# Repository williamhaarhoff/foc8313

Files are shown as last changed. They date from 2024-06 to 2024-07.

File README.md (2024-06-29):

# foc8313
This board was inspired by [Foc-Ctrl-Lite](https://github.com/peng-zhihui/Ctrl-FOC-Lite). FOC8313 is a highly compact, feature rich, daisy-chainable,  field oriented control board based around the DRV8313 3 phase half bridge driver. This board is highly configurable and upgradeable, and includes all the manufacturing files required start producing controllers for $\approx$ $20/board
|Front|Back|
|--| --|
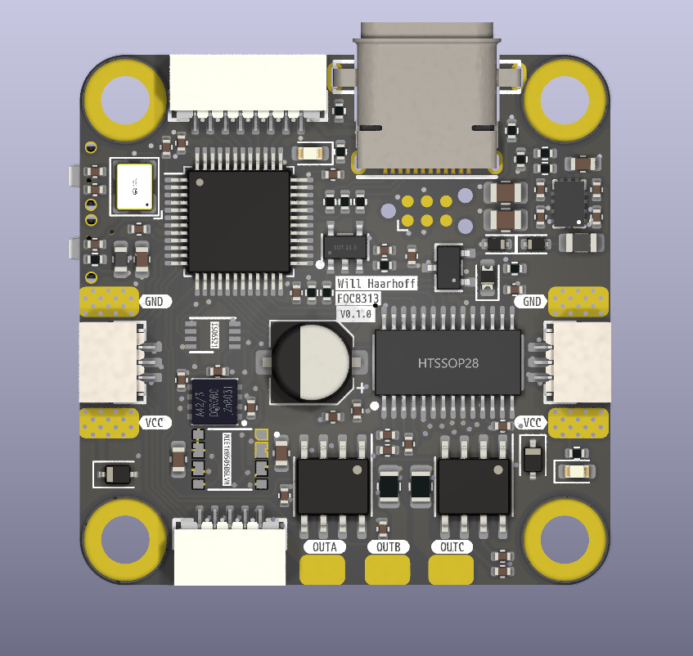
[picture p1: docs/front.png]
front
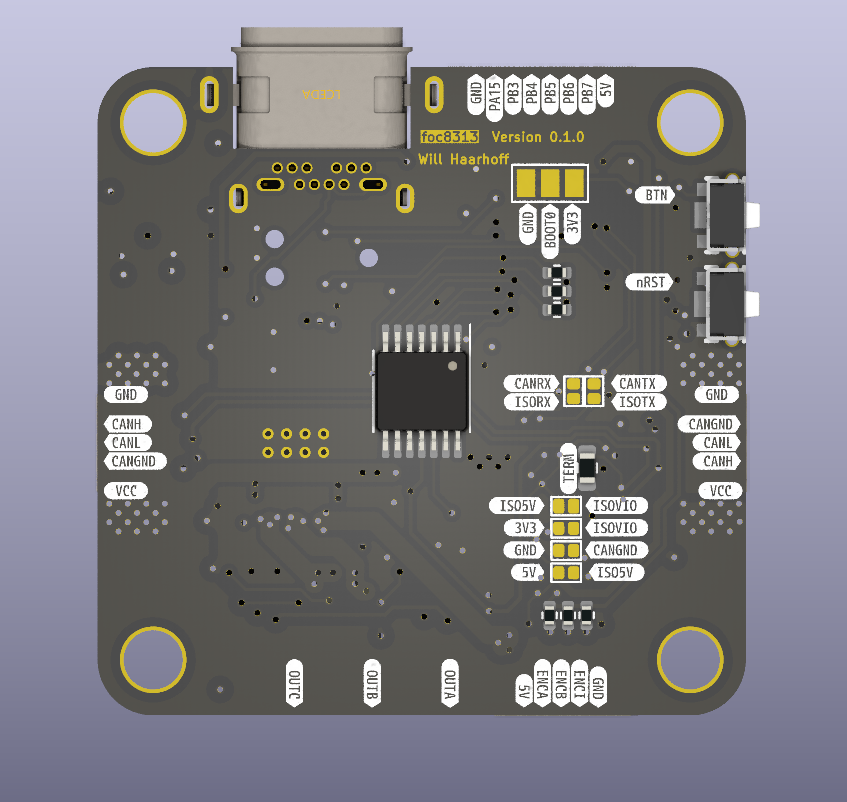
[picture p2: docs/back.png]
back
| | |

## Features:
 - Highly compact 35x35mm outline
 - 29x29 square M3 hole pattern
 - 12V to 35V operating range
 - 3.5A max per phase current
 - Onboard STM32F103CBTx microcontroller
 - Based on the DRV8313 3 phase half bridge driver
 - 2 x INA240A2D high side current sense amplifiers
 - 1 x AS5047D back mounted hall effect encoder
 - EEPROM to store configurations / calibrations etc. 
 - Daisy chainable power and CAN
 - Programmable with USB-DFU or StLink - 6 pin tag connect
 - Auxilliary encoder/Timer port with 5V and GND
 - Auxilliary SPI/GPIO and I2C/UART port with 5V and GND
 - Easily upgradable for isolated CAN (3 wire)
 - Extremely compact isolated CAN
 - JLC manufacturing files included
 - Cost optimised for PCBA with JLCPCB (as few extended components as possible)
 - Most basic variant costs $\approx$ $20 per board (for 10 PCBs at JLCPCB)
 - Predominantly single sided design allows for cost effective single sided PCBA, easy hot plating for rework, easy configuration with jumpers

| Top | In1 |
|--| --|
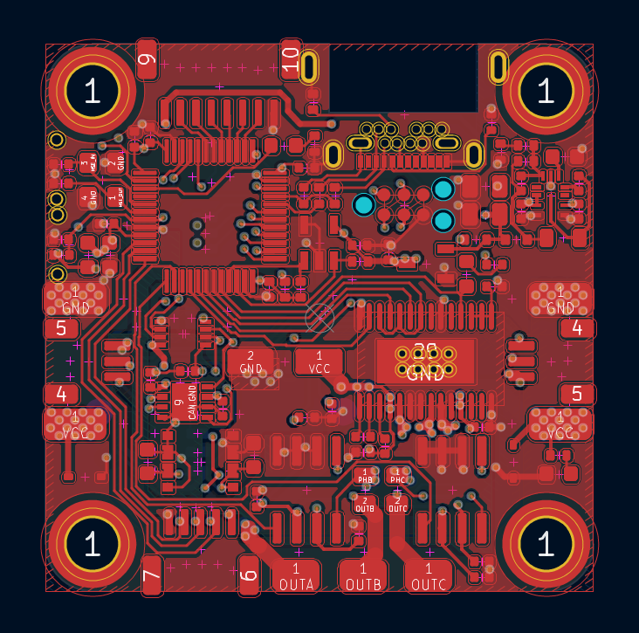
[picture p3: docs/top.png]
top
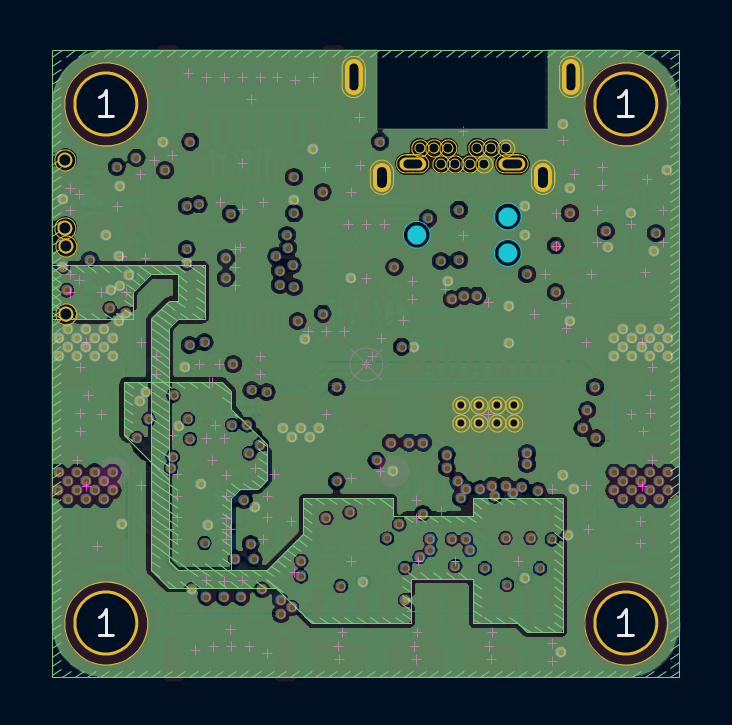
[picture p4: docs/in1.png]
in1
|||
|In2 | Bottom|
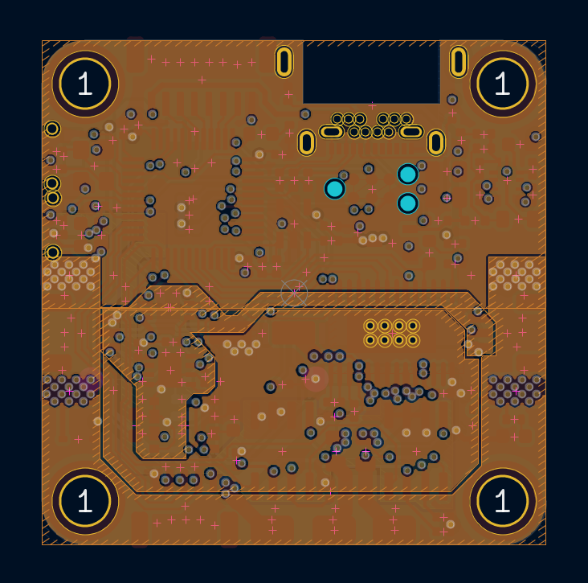
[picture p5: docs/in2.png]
in2
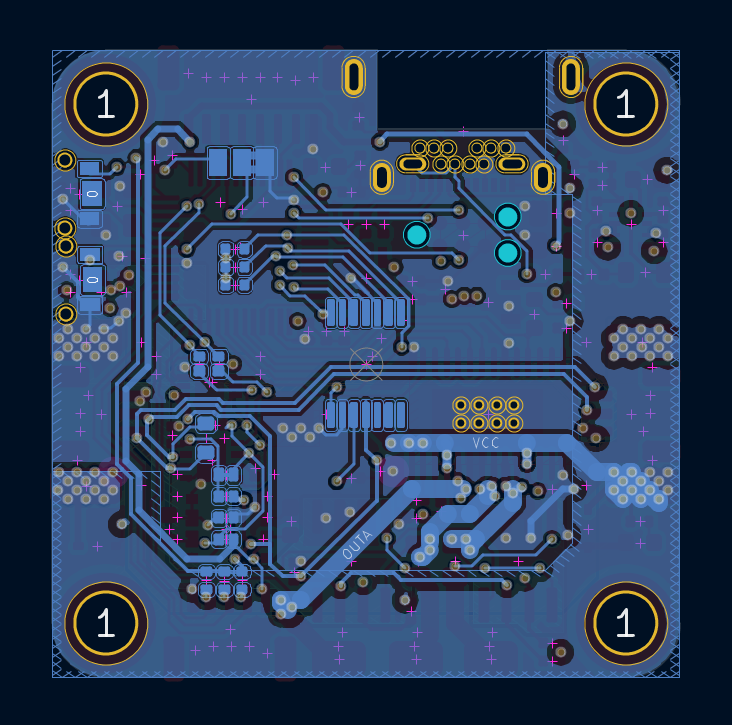
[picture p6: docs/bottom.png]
bottom
|||

# PCBA - Cost Scaling:
| Version | Colour | Finish | Assembly | Quantity | Unit price | Extended Price |
| ----- | ---- | --- | ----- | ----- | ---- | --- |
| v1.0 | Black  | Enig | Standard T&B  | 15 |$30.8 | $462.57 |
| v1.0 | Black  | Enig | Standard Top  | 15 |$24.3 | $364.22 |
| v1.0 | Black  | HASL | Standard Top  | 10 |$24.75 | $247.51 |
| v1.0 | Black  | Enig | Standard T&B  | 100 |$16.78 | $1678.39 |
| v1.0 | Green  | HASL | Economic Top  | 2 |$53.45 | $106.89 |
| v1.0 | Green  | HASL | Economic Top  | 5 |$30.28 | $151.40 |
| v1.0 | Green  | HASL | Economic Top  | 10 |$20.48 | $204.81 |
| v1.0 | Green  | HASL | Economic Top  | 15 |$19.2 | $288.48 |
| v1.0 | Green  | HASL | Economic Top  | 30 |$15.6 | $468.48 |
| v1.0 | Green  | HASL | Standard Top  | 100 |$12.98 | $1297.77 |
| v1.0 | Black  | Enig | No ICs Top | 10 |$15.9 + | $159.37 |
| v1.0 | Black  | Enig | No ICs Top | 15 |$12.9 + | $193.44 |

# ICs:
15x @LCSC: 215.22 -> 14.33
10x @LCSC: 146.71 -> 14.6

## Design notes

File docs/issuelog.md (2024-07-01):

# v0.1.0 - issues
  - USB incorrect outline
  - USB incorrect pinout 
  - 3.3v vs 3v3 mixed incorrect nets
  - LDO incorrect pinout
  - ISO power vselect incorrect
  - Some boards had buck converter shorts
  - ISO power too close to CAN IC
  - Capacitor too close to CAN IC
  - Diode inline with buck converter output
  - Vcc power plane gets choked and should be wider
  - Daisy chained GND also gets choked and should be wider
  - Plane clearance is very small
  - Isense resistors could be bigger
  - No vbus measurement
  - Silk screen too small
  - Not a fan of the yellow or red LEDs
  - Provision pullups for external ABI interface?

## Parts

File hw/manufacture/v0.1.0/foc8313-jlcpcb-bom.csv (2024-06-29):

Comment | Designator | Footprint | LCSC Part Number
100n | C1,C2,C3,C4,C6,C7,C12,C20,C21,C22,C24,C25,C26,C27,C28,C29,C33,C34,C35,C36 | C_0402_1005Metric | C307331
1u | C5,C15 | C_0603_1608Metric | C15849
220n | C8 | C_0402_1005Metric | C16772
2.2u | C9 | C_0805_2012Metric | C377773
22n | C10,C11 | C_0402_1005Metric | C1532
4.7p | C13 | C_0402_1005Metric | C1567
22u | C14 | C_0805_2012Metric | C45783
18p | C16,C17 | C_0402_1005Metric | C1549
2.2u | C18 | C_0402_1005Metric | C12530
10n | C23 | C_0402_1005Metric | C15195
47u | C30 | CP_Elec_5x5.7 | C7471868
22u | C37,C38 | C_0603_1608Metric | C59461
36V | D1,D3 | D_SOD-323 | C92677
RB521S30T1G | D2,D6 | D_SOD-523 | C145179
LED | D4 | D_0603_1608Metric | C2286
WHITE | D5 | LED_0603_1608Metric | C2290
YELLOW | D7 | LED_0603_1608Metric | C72038
MountingHole_Pad | H1,H2,H3,H4 | 2x4 | no_part_number
MountingHole_Pad | H5,H6,H9 | 2x3 | no_part_number
MountingHole | H7,H8,H10,H11 | MountingHole_3.2mm_M3_DIN965_Pad_TopOnly | no_part_number
Tag Connect | J1 | Tag-Connect_TC2030-IDC-NL_2x03_P1.27mm_Vertical | no_part_number
Encoder | J2 | CONN-SMD_5P-P1.00_MEGASTAR_ZX-SH1.0-5PWT | C7430447
CAN | J3,J4 | CONN-SMD_AFC10-S03QCA-00 | C2764182
GPIO | J6 | CONN-SMD_8P-P1.00_MEGASTAR_ZX-SH1.0-8PWT | C7430450
* | JP1 | SolderJumper-3_P1.3mm_Bridged2Bar12_Pad1.0x1.5mm | no_part_number
* | JP2,JP4,JP5,JP6,JP7 | jumper12_open | no_part_number
* | JP3 | jumper12_closed | no_part_number
27n | L1 | L_0603_1608Metric | C280267
10u | L2 | L_0805_2012Metric | C285963
MIE1W0505BGLVH-3R-Z | PS1 | CONV_MIE1W0505BGLVH-3R-Z | no_part_number
100k | R1,R3 | R_0402_1005Metric | C25741
120 | R2 | R_0603_1608Metric | C22787
20k | R4,R7 | R_0402_1005Metric | C25765
10k | R5,R9,R10 | R_0402_1005Metric | C25744
1k5 | R6,R8,R17 | R_0402_1005Metric | C25867
22 | R11,R16 | R_0402_1005Metric | C25092
6m | R12,R13 | R_0805_2012Metric | C728268
5.1k | R14,R15 | R_0402_1005Metric | C25905
4.7k | R18 | R_0402_1005Metric | C25900
SW_SPST | SW1,SW2 | SW-TH_PANASONIC_EVPAKE31A | C569760
LMR36015SFBRNXR | U1 | VQFN-12_L3.0-W2.0-P0.65-BL_TI_RNX | C3187929
XC6206P332MR | U2 | SOT-23-3_L2.9-W1.6-P1.90-LS2.8-BR | C5446
DRV8313PWP | U3 | HTSSOP-28_L9.8-W4.5-P0.65-LS6.6-BL-EP | C92482
STM32F103CBTx | U4 | LQFP-48_7x7mm_P0.5mm | C8304
AS5047D | U5 | TSSOP-14_4.4x5mm_P0.65mm | C962063
ZD24C08AE1-STGMT | U6 | SOT-23-5_L3.0-W1.7-P0.95-LS2.8-BL | C3007877
INA240A2D | U7,U8 | SOIC-8_3.9x4.9mm_P1.27mm | C2060768
ISO6521F | U10 | DFN-8-1EP_3x2mm_P0.5mm_EP1.3x1.5mm | no_part_number
TJA1051TK/3,118 | U12 | HVSON-8_L3.0-W3.0-P0.65-BL-EP | C124020
USB3.1-TYPE-C-FSABC | USB1 | USB-3.1-SMD_USB3.1-TYPE-C-FSABC | C319140
X322516MLB4SI | X1 | OSC-SMD_4P-L3.2-W2.5-BL | C13738

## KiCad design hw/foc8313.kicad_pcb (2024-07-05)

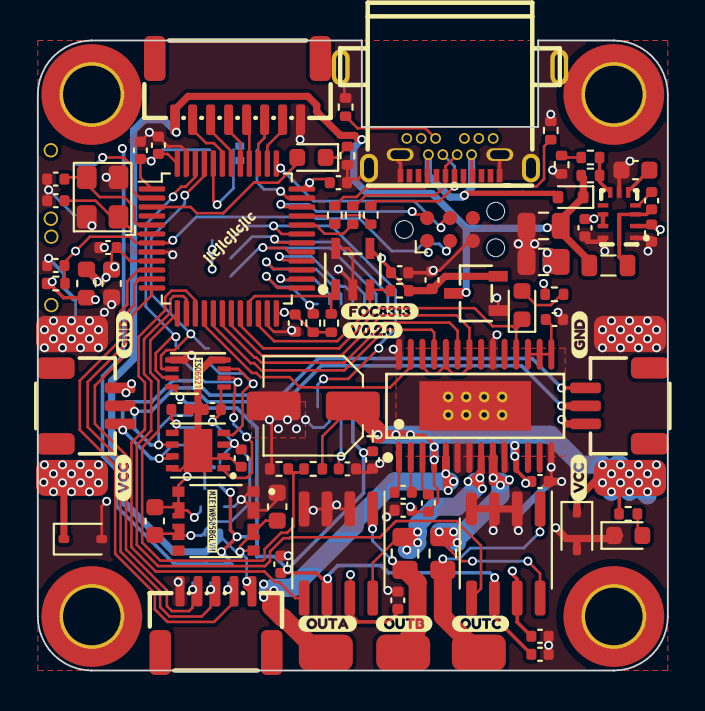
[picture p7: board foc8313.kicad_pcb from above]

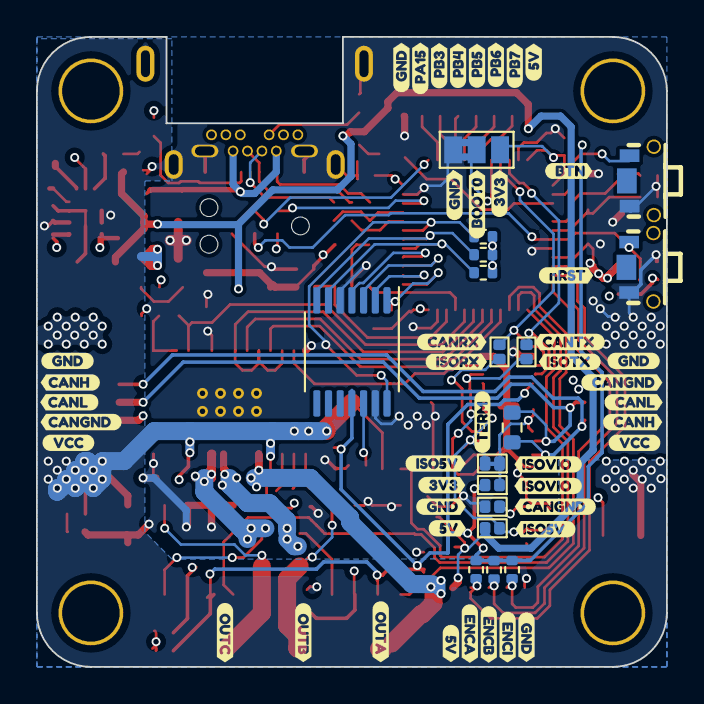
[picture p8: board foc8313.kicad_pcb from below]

Board: 4 copper layers, 35.0 x 35.0 mm, 161 parts (61 on the bottom side), 73 nets.

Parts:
C1, C2, C3, C4, C6, C7, C12, C20, C21, C22, C24, C25, C26, C27, C28, C29, C33, C34, C35, C36: 100n; C_0402_1005Metric
C5, C15: 1u; C_0603_1608Metric
C8: 220n; C_0402_1005Metric
C9: 2.2u; C_0805_2012Metric
C10, C11: 22n; C_0402_1005Metric
C14: 22u; C_0805_2012Metric
C16, C17: 18p; C_0402_1005Metric
C18: 2.2u; C_0402_1005Metric
C23: 10n; C_0402_1005Metric
C30: 47u; CP_Elec_5x5.7
C37, C38: 22u; C_0603_1608Metric
D1, D3: 36V; D_SOD-323
D4: LED; D_0603_1608Metric
D5: WHITE; LED_0603_1608Metric
D6: RB521S30T1G; D_SOD-523
D7: YELLOW; LED_0603_1608Metric
H1, H2, H3, H4: MountingHole_Pad; 2x4
H5, H6, H9: MountingHole_Pad; 2x3
H7, H8, H10, H11: MountingHole; MountingHole_3.2mm_M3_DIN965_Pad_TopOnly
J1: Tag Connect; Tag-Connect_TC2030-IDC-NL_2x03_P1.27mm_Vertical
J2: Encoder; CONN-SMD_5P-P1.00_MEGASTAR_ZX-SH1.0-5PWT
J3, J4: CAN; CONN-SMD_AFC10-S03QCA-00
J6: GPIO; CONN-SMD_8P-P1.00_MEGASTAR_ZX-SH1.0-8PWT
JP1: *; SolderJumper-3_P1.3mm_Bridged2Bar12_Pad1.0x1.5mm
JP2, JP4, JP5, JP6, JP7: *; jumper12_open
JP3: *; jumper12_closed
L1: 27n; L_0603_1608Metric
L2: 10u; L_0805_2012Metric
PS1: MIE1W0505BGLVH-3R-Z; CONV_MIE1W0505BGLVH-3R-Z
R1, R3, R25: 100k; R_0402_1005Metric
R2: 120; R_0603_1608Metric
R4, R7: 20k; R_0402_1005Metric
R5, R9, R10, R26: 10k; R_0402_1005Metric
R6, R8, R17: 1k5; R_0402_1005Metric
R11, R16: 22; R_0402_1005Metric
R12, R13: 10m; R_0805_2012Metric
R14, R15, R19, R20, R21, R22, R23, R24: 5.1k; R_0402_1005Metric
R18: 4.7k; R_0402_1005Metric
SW1, SW2: SW_SPST; SW-TH_PANASONIC_EVPAKE31A
U1: LMR36015SFBRNXR; VQFN-12_L3.0-W2.0-P0.65-BL_TI_RNX
U2: XC6206P332MR; SOT-23-3_L2.9-W1.6-P1.90-LS2.8-BR
U3: DRV8313PWP; HTSSOP-28_L9.8-W4.5-P0.65-LS6.6-BL-EP
U4: STM32F103CBTx; LQFP-48_7x7mm_P0.5mm
U5: AS5047D; TSSOP-14_4.4x5mm_P0.65mm
U6: ZD24C08AE1-STGMT; SOT-23-5_L3.0-W1.7-P0.95-LS2.8-BL
U7, U8: INA240A2D; SOIC-8_3.9x4.9mm_P1.27mm
U10: ISO6521F; DFN-8-1EP_3x2mm_P0.5mm_EP1.3x1.5mm
U12: TJA1051TK/3,118; HVSON-8_L3.0-W3.0-P0.65-BL-EP
USB1: USB3.1-TYPE-C-FSABC; USB-3.1-SMD_USB3.1-TYPE-C-FSABC
X1: X322516MLB4SI; OSC-SMD_4P-L3.2-W2.5-BL
kibuzzard-6687B96D: G***; kibuzzard-6687B96D
kibuzzard-6687B97C: G***; kibuzzard-6687B97C
kibuzzard-6687B916, kibuzzard-6687B916#2, kibuzzard-6687B916#3, kibuzzard-6687B916#4: G***; kibuzzard-6687B916
kibuzzard-6687B962: G***; kibuzzard-6687B962
kibuzzard-6687B975: G***; kibuzzard-6687B975
kibuzzard-6687B983: G***; kibuzzard-6687B983
kibuzzard-6687B989: G***; kibuzzard-6687B989
kibuzzard-6687B990, kibuzzard-6687B990#2: G***; kibuzzard-6687B990
kibuzzard-6687BB13: G***; kibuzzard-6687BB13
kibuzzard-6687BB22: G***; kibuzzard-6687BB22
kibuzzard-6687BB56: G***; kibuzzard-6687BB56
kibuzzard-6687BB64: G***; kibuzzard-6687BB64
kibuzzard-6687BBB1: G***; kibuzzard-6687BBB1
kibuzzard-6687BBBA: G***; kibuzzard-6687BBBA
kibuzzard-6687BBC5: G***; kibuzzard-6687BBC5
kibuzzard-6687BC5B: G***; kibuzzard-6687BC5B
kibuzzard-6687BC6D: G***; kibuzzard-6687BC6D
kibuzzard-6687BC64: G***; kibuzzard-6687BC64
kibuzzard-6687BCF3, kibuzzard-6687BCF3#2: G***; kibuzzard-6687BCF3
kibuzzard-6687BD2B, kibuzzard-6687BD2B#2: G***; kibuzzard-6687BD2B
kibuzzard-6687BD8E, kibuzzard-6687BD8E#2: G***; kibuzzard-6687BD8E
kibuzzard-6687BD9D: G***; kibuzzard-6687BD9D
kibuzzard-6687BD69: G***; kibuzzard-6687BD69
kibuzzard-6687BD70: G***; kibuzzard-6687BD70
kibuzzard-6687BD76: G***; kibuzzard-6687BD76
kibuzzard-6687BD97: G***; kibuzzard-6687BD97
kibuzzard-6687BF5D: G***; kibuzzard-6687BF5D
kibuzzard-6687BF56: G***; kibuzzard-6687BF56
kibuzzard-6687BFAE: G***; kibuzzard-6687BFAE
kibuzzard-6687BFB6: G***; kibuzzard-6687BFB6
kibuzzard-6687BFD2: G***; kibuzzard-6687BFD2
kibuzzard-6687BFE6: G***; kibuzzard-6687BFE6
kibuzzard-6687C00C, kibuzzard-6687C00C#2: G***; kibuzzard-6687C00C
kibuzzard-6687C0E6: G***; kibuzzard-6687C0E6
kibuzzard-6687C3AC, kibuzzard-6687C3AC#2: G***; kibuzzard-6687C3AC
kibuzzard-6687C4B0: G***; kibuzzard-6687C4B0
kibuzzard-6687C4F0: G***; kibuzzard-6687C4F0
kibuzzard-6687C12A: G***; kibuzzard-6687C12A
kibuzzard-6687C148: G***; kibuzzard-6687C148
kibuzzard-6687C371, kibuzzard-6687C371#2: G***; kibuzzard-6687C371
kibuzzard-6687C408: G***; kibuzzard-6687C408
kibuzzard-6687C440: G***; kibuzzard-6687C440
kibuzzard-6687C487: G***; kibuzzard-6687C487
kibuzzard-663606F1: G***; kibuzzard-663606F1
kibuzzard-6636082D: G***; kibuzzard-6636082D

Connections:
+3.3V: C1.1, C2.1, C3.1, C4.1, C18.1, C25.1, C26.1, C28.1, C36.1, J1.1 (VCC), JP1.3 (B), JP5.1 (A), L1.2, R1.1, R5.2, R6.1, R9.1, R10.1, R19.2, R20.2, R21.2, R22.2, R23.2, R24.2, U2.2 (Vout), U4.1 (VBAT), U4.24 (VDD), U4.36 (VDD), U4.48 (VDD), U5.11 (VDD), U6.4 (VCC), U7.6 (V+), U8.6 (V+), U10.8 (VCC2)
+3.3VA: C5.1, C6.1, C27.1, C29.1, L1.1, U4.9 (VDDA), U7.7 (REF1), U8.7 (REF1)
+5V: C14.1, C37.1, D6.1 (K), J2.5, J6.8, JP4.1 (A), L2.1, PS1.8 (EN), PS1.9_10 (VIN), R3.1, U2.3 (Vin)
+5VD: D6.2 (A), R17.2, USB1.A4 (VBUS), USB1.A9 (VBUS), USB1.B4 (VBUS), USB1.B9 (VBUS)
/BOOT0: JP1.2 (C), U4.44 (BOOT0)
/CAN.GND: C33.2, C34.2, C35.2, C38.2, J3.1, J4.1, JP2.2 (B), PS1.2 (GND2), PS1.3_4 (GND2), U10.4 (GND1), U12.2 (GND), U12.8 (S), U12.9 (EP)
/CAN.H: J3.3, J4.3, R2.1, U12.7 (CANH)
/CAN.L: J3.2, J4.2, R2.2, U12.6 (CANL)
/CAN.RX: JP7.1 (A), U4.45 (PB8), U10.6 (OUTB)
/CAN.TX: JP6.1 (A), U4.46 (PB9), U10.7 (INA)
/COM1: J6.7, U4.43 (PB7)
/COM2: J6.6, U4.42 (PB6)
/DRV_EN: U3.22 (EN3), U3.24 (EN2), U3.26 (EN1), U4.19 (PB1)
/DRV_INA: U3.27 (IN1), U4.16 (PA6)
/DRV_INB: U3.25 (IN2), U4.17 (PA7)
/DRV_INC: U3.23 (IN3), U4.18 (PB0)
/ENC1_A: R22.1, U4.30 (PA9), U5.7 (A)
/ENC1_B: R23.1, U4.29 (PA8), U5.6 (B)
/ENC1_Z: R24.1, U4.31 (PA10), U5.14 (I/PWM)
/ENC2_A: J2.4, R19.1, U4.10 (PA0)
/ENC2_B: J2.3, R20.1, U4.11 (PA1)
/ENC2_Z: J2.2, R21.1, U4.12 (PA2)
/GPIO1: J6.5, U4.41 (PB5)
/GPIO2: J6.4, U4.40 (PB4)
/GPIO3: J6.3, U4.39 (PB3)
/GPIO4: J6.2, U4.38 (PA15)
/HSE_IN: C17.1, U4.5 (PD0), X1.3
/HSE_OUT: C16.2, U4.6 (PD1), X1.1
/I2C2.SCL: R9.2, U4.21 (PB10), U6.1 (SCL)
/I2C2.SDA: R10.2, U4.22 (PB11), U6.3 (SDA)
/ISENSE_B: U4.15 (PA5), U8.5
/ISENSE_C: U4.14 (PA4), U7.5
/OUTA: H5.1, U3.5 (OUT1)
/OUTB: H6.1, R13.2, U8.1 (-)
/OUTC: H9.1, R12.2, U7.1 (-)
/PHB: R13.1, U3.8 (OUT2), U8.8 (+)
/PHC: R12.1, U3.9 (OUT3), U7.8 (+)
/SPI2_MISO: U4.27 (PB14), U5.3 (MISO)
/SPI2_MOSI: U4.28 (PB15), U5.4 (MOSI)
/SPI2_SCK: U4.26 (PB13), U5.2 (CLK)
/STATUS: D5.2 (A), U4.3 (PC14)
/SWCLK: J1.4 (SWCLK), U4.37 (PA14)
/SWDIO: J1.2 (SWDIO), U4.34 (PA13)
/USB_DM: R16.1, U4.32 (PA11)
/USB_DM_EXT: R16.2, USB1.A7 (DN1), USB1.B7 (DN2)
/USB_DP: R11.1, R17.1, U4.33 (PA12)
/USB_DP_EXT: R11.2, USB1.A6 (DP1), USB1.B6 (DP2)
/VSENSE: R25.2, R26.2, U4.13 (PA3)
/isocan/ISO5V: C33.1, C35.1, C38.1, JP3.2 (B), JP4.2 (B), PS1.5_6 (VOUT), U10.1 (VCC1), U12.3 (VCC)
/isocan/ISORX: JP7.2 (B), U10.3 (INB), U12.4 (RXD)
/isocan/ISOTX: JP6.2 (B), U10.2 (OUTA), U12.1 (TXD)
/isocan/ISOVIO: C34.1, JP3.1 (A), JP5.2 (B), U12.5 (VIO)
/~BTN: SW1.1 (A), U4.2 (PC13)
/~DRV_NFAULT: D4.1 (K), U3.18 (~FAULT), U4.20 (PB2)
/~DRV_NRST: C8.1, U3.15 (V3P3), U3.16 (~RESET), U3.17 (~SLEEP)
/~NRST: C7.1, J1.3 (~RESET), R1.2, SW2.1 (A), U4.7 (NRST)
/~SPI2_NSS: R5.1, U4.25 (PB12), U5.1 (~CS)
GND: C1.2, C2.2, C3.2, C4.2, C5.2, C6.2, C7.2, C8.2, C9.2, C10.2, C11.2, C14.2, C15.2, C16.1, C17.2, C18.2, C20.2, C21.2, C24.2, C25.2, C26.2, C27.2, C28.2, C29.2, C30.2, C36.2, C37.2, D1.2 (A2), D3.2 (A2), D7.1 (K), H2.1, H4.1, J1.5 (GND), J2.1, J6.1, JP1.1 (A), JP2.1 (A), PS1.1 (GND1), PS1.11_12 (GND1), R4.2, R8.2, R14.2, R15.2, R26.1, SW1.2 (B), SW2.2 (B), U1.1 (PGND), U1.6 (AGND), U1.11 (PGND), U2.1 (GND), U3.6 (PGND1), U3.7 (PGND2), U3.10 (PGND3), U3.14 (GND), U3.20 (GND), U3.28 (GND), U3.29 (EXP), U4.8 (VSSA), U4.23 (VSS), U4.35 (VSS), U4.47 (VSS), U5.5 (TST), U5.13 (GND), U6.2 (GND), U6.5 (WP), U7.2 (GND), U7.3 (REF2), U7.4 (GND), U8.2 (GND), U8.3 (REF2), U8.4 (GND), U10.5 (GND1), USB1.A1 (GND), USB1.A12 (GND), USB1.B1 (GND), USB1.B12 (GND), USB1.SHELL, X1.2, X1.4
unnamed: D4.2 (A), R6.2
unnamed: D5.1 (K), R8.1
unnamed: D7.2 (A), R7.2
unnamed: R4.1, R18.2
unnamed: C12.2, U1.4 (BOOT)
unnamed: R3.2, R18.1, U1.7 (FB)
unnamed: C12.1, L2.2, U1.3 (NC), U1.12 (SW)
unnamed: C15.1, U1.5 (VCC)
unnamed: C23.2, U3.2 (CPH)
unnamed: C23.1, U3.1 (CPL)
unnamed: C22.2, U3.3 (VCP)
unnamed: C24.1, U5.12 (VDD3V3)
unnamed: R14.1, USB1.A5 (CC1)
unnamed: R15.1, USB1.B5 (CC2)
VCC: C9.1, C10.1, C11.1, C20.1, C21.1, C22.1, C30.1, D1.1 (A1), D3.1 (A1), H1.1, H3.1, R7.1, R25.1, U1.2 (VIN), U1.9 (EN), U1.10 (VIN), U3.4 (VM), U3.11 (VM)

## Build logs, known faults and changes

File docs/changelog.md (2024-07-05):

v0.2.0
- Removed compensation capacitor, not required
- Removed power orring diode on buck converter side of cap
- Fixed separate +3.3V and 3V3 nets
- LDO pinout corrected, swapped pin 2 and 3 in symbol
- Enlarged USBC cutout so connector can mount properly
- Isolated power supply to generate 5V instead of 3.3V (VSEL floating)
- Fixed USBC symbol pinout to be correct
- 6m current shunt to 10m
- NC pin 3 of buck controller connected to SW for better routing of bootstrap cap
- Vcc monitoring with resistor divider
- Unpinching Vcc to 3.4mm
- Unpinching GND for daisy chain
- Increased most plane clearances
- Tweaked plane geometry to better follow referenced tracks
- Silk screen labels using bold larger font

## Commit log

2024-06-29 [hw] Setting up project, starting to layout schematic
    [foc8313.kicad_pcb, foc8313.kicad_sch]
2024-06-29 [Hw] 5V buck, Isocan, Encoder, MCU, with LCSC parts
    [foc8313.kicad_pcb, foc8313.kicad_sch, isense.kicad_sch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]
2024-06-29 WIP XT30?
    [foc8313.kicad_pcb, foc8313.kicad_sch, isocan.kicad_sch]
2024-06-29 [Hw] No iso can, 0402 where possible, approx layout and formfactor
    [foc8313.kicad_pcb, foc8313.kicad_sch, isense.kicad_sch]
2024-06-29 [Hw] Rough incomplete layout and component placement
    [foc8313.kicad_pcb, foc8313.kicad_sch]
2024-06-29 [Hw] Decent current sense layout
    [foc8313.kicad_pcb]
2024-06-29 [Hw] compact discrete 4 wire iso can, approx drv routing, eeprom
    [foc8313.kicad_pcb, foc8313.kicad_sch, isocan.kicad_sch]
2024-06-29 [Hw] Squeezing in push button and aux 8 pin connector
    [foc8313.kicad_pcb, foc8313.kicad_sch]
2024-06-29 [Hw] Tiny eeprom, all components fit on board!
    [foc8313.kicad_pcb, foc8313.kicad_sch, isocan.kicad_sch]
2024-06-29 [Hw] Simplifying CAN
    [foc8313.kicad_pcb, foc8313.kicad_sch, isocan.kicad_sch]
2024-06-29 [Hw] Cleaning up 5V section
    [foc8313.kicad_pcb, foc8313.kicad_sch]
2024-06-29 [Hw] User button, tag connect placement, eeprom placement
    [foc8313.kicad_pcb, foc8313.kicad_sch]
2024-06-29 [Hw] Small ICs to make 3 wire can possible in this formfactor
    [foc8313.kicad_pcb, foc8313.kicad_sch, isense.kicad_sch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]
2024-06-29 [Hw] USBC fixes, 3 wire can, encoder and comms headers
    [foc8313.kicad_sch, isocan.kicad_sch]
2024-06-29 [Hw] Optimised pin out for routing, new layout
    [foc8313.kicad_pcb, foc8313.kicad_sch, isocan.kicad_sch]
2024-06-29 [Hw] Routing topology complete
    [foc8313.kicad_pcb, foc8313.kicad_sch, isocan.kicad_sch]
2024-06-29 [Hw] Untangled isolation jumpers
    [foc8313.kicad_pcb]
2024-06-29 [Hw] Aligned DRV IC, thick power traces
    [foc8313.kicad_pcb]
2024-06-29 [Hw] Added labels to silkscreen
    [foc8313.kicad_pcb, foc8313.kicad_sch]
2024-06-29 [Hw] All connections completed - only DRC left
    [foc8313.kicad_pcb, foc8313.kicad_sch]
2024-06-29 [Hw] Optimised components for JLC basic parts
    [foc8313.kicad_pcb, foc8313.kicad_sch, isense.kicad_sch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]
2024-06-29 [Hw] Version 0.1.0 - sent for manufacture
    [foc8313-jlcpcb-bom.csv, foc8313.kicad_pcb, foc8313.kicad_sch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]
2024-06-30 [Hw] WIP begun revisions for v0.2.0
    [foc8313.kicad_pcb, foc8313.kicad_sch, isense.kicad_sch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]
2024-07-01 [Hw] Unpinched Vcc to 3.4mm width
    [foc8313.kicad_pcb, foc8313.kicad_sch, isocan.kicad_sch]
2024-07-05 [Hw] Plane geometry changes, more legible silkscreen
    [foc8313.kicad_pcb]
